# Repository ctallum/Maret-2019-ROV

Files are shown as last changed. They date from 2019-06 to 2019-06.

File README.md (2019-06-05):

# Maret 2019 ROV
In this Git Hub, I will try to provide all the needed code, 3d model files, and instructions needed to either build or fix the 2019 ROV. 

## Code
### Setting up the Rasperry Pi 

To set up the Rasperry pi, first make sure the Pi has a static IP adress. If it does, skip ahead. If it doesn not, you will not be able to ssh into the Pi. To set a static IP address, first type the following into the Pi terminal.
```bash
sudo nano /etc/dhcpcd.conf
```
At the bottom of the config file, type the following:
```bash
interface eth0
static ip_address=169.254.38.217/24
```
This should create a static IP address on the Pi. (The IP adress doesn't need to be the one written above. If you make your own, just make sure to change the code in the Poolside.pde to reflect this). You can check everything works by typing the following into the terminal.
```bash
ifconfig
```
Under eth0, it should report the static IP.

The next step is to make sure the Pi has all the needed python libraries. You will need Nanpy and Flask. To install Nanpy, type the follwing into the terminal.
```bash
sudo pip3 install nanpy
```
To install Flask, type the following into the terminal. 
```bash
sudo pip3 install flask
```
There are many installation guides online (including the one on Flask's website) that involve the creation of virtual enviorments for python. This is not nescessary. Disreagard these guides and just install flask with the above method. 

To finally get the code up and running, on the Raspberry Pi desktop, you will need the folder titled "New". This folder contains all the Pi code to get the craft running. I will include this folder with all its contents in the GitHub. All the code is written to be run in python. 

### Setting up the Surface Computer
On the surface computer, you will need the folder titled "Poolside". This folder contains all the code that runs on the surface. I will also include this folder with all its contents in the GitHub. The "poolside" code runs in a program called Processing, so also download that. In Processing, you will need to add the following libraries: G4P, Game Control Plus, and HTTP Requests for Processing. Adding these libraries is really easy. In processing, "Open Library" --> "Add library...". From here you can search up each library and add them. You need to install the Xbox controller drivers. 
- https://processing.org/
- https://www.techspot.com/drivers/driver/file/information/15363/

### Setting up the Arduino
Contrary to popular beleif (or at least what we thought we knew) you do indeed need to set up Nanpy code on the Arduino. You can follow the guide below for full instructions on installing the nanpy code on the Arduino. 
- https://nanpy.github.io/

Alternativly, you could plug the current arduino into a laptop, open up the Arduino software, save the contents as an ide. and then copy the code onto another Arduino. (I haven't tried this in person, but I think it would work, and it would save you a bit of time).

# Running the ROV

First, make sure everything is properly connected. In the ROV, the camera should be plugged in fully (and beleive me, it is easier to check now than it is to change it later once the dome is on). On the surface, the ethernet and Xbox controller should be plugged into the surface laptop. The tether should be plugged into 12 volts.
 
The first step in running the ROV is to run the code on the Pi. Since the Pi is on the craft, you must run the code remotely. This is done via ssh. On a windows machine, one could use a program such as Putty to ssh to the Pi, however, on a Mac, you can use the built in Terminal. 

First, establish connection with the Pi. 
```bash
ssh pi@169.254.38.217
```
169.254.38.217 is the static IP address of the Pi we have used in years past. However, if the physical Pi changes or you change the software, the IP may be different. You can always find the IP address of the Pi by typing "ifconfig" into the Pi terminal. You can also change the physical IP adress of the Pi by edditing the dhcpcd.conf file (see the link below). (Also see above).
- https://www.modmypi.com/blog/how-to-give-your-raspberry-pi-a-static-ip-address-update

Once you have connected to the Pi, it will request a password. On a new Pi, the default password is "raspberry". However, if Chris L. is the one who set it up, the password will probably be "hi".

Once you are into the Pi, you need to access the run file.
```bash
cd Desktop/New/ROV
```

This will put you inside the ROV subfile within the New folder. Inside this folder is the file App.py. This is the main code which runs the ROV. Run this file.
```bash
python3 App.py
```

As the file runs, the Terminal screen will display what is currently going on. It should say something along the lines of setting up a nanpy connection and running a flask server on the ip address "0.0.0.0:5000". (Don't worry that it says 0.0.0.0 and not the IP adress of the Pi, this if fine. 0.0.0.0 is the local adress of the Pi which is the IP you set). The Terminal screen is also the Debugger window, so if anything goes wrong, it will tell you. Keep this window up. 

After you have run the Pi code, you need to run the Poolside code. To do this, open the PoolSide folder and open the file titled PoolSide.pde. This file should open up in Processing. In processing, click the "Run" button. This should bring up a small window that gives the readings of all the motor values. 

To get the video streaming site up, go to your web browser and type in:
```bash
http://169.254.175.59:5000
```
This should open up a webpage with the live video stream. 

### Tips and other helpful bits
- When trying to ssh into the Pi, it may not be immediate. Just spam the ssh request until it goes through.
- If you you are testing the Pi out (and the Pi is not in the tube), you can run the program manually without ssh. To do that, hook up a monitor and keyboard/mouse to the pi. You can edit the code by oppening the App.py file in the python scrip editor, but you cannot run it like you might be used to doing with any other python program. If you run it from the python scrip editor, you cannot stop the program from running without rebooting the Pi. If you want to run it to test it out (or test out any changes you made to it), you have to run it from the terminal. 
```bash
cd Desktop/New/ROV
python3 App.py
```
- Always run the poolside code after the Pi code is running. 
- I don't think it is nescessary to runn the poolside code to access the live video stream, but that is the only thing you can do. 

# Electronics

## Componenents
- Rasperry Pi [buy link](https://www.amazon.com/ELEMENT-Element14-Raspberry-Pi-Motherboard/dp/B07BDR5PDW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)
- Arduino Mega [buy link](https://www.amazon.com/Elegoo-EL-CB-003-ATmega2560-ATMEGA16U2-Arduino/dp/B01H4ZLZLQ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)
- Pololu mc33926 motor drivers (x6) [buy link](https://www.pololu.com/product/1212)
- 12v to 5v buck step down converter (x2) [buy link](https://www.amazon.com/DROK-Electric-Converter-Step-down-Regulator/dp/B00C63TLCC?ref_=fsclp_pl_dp_2)
- dsn-vc288 Volt Amp Meter [buy link](https://www.amazon.com/McIgIcM-Digital-Voltmeter-Ammeter-10ADetector/dp/B06XR2XKNT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)
- Screw terminals [buy link](https://www.amazon.com/Eowpower-Position-Terminal-Insulated-Barrier/dp/B06XKFCTSM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)

## What they do
Rasperry Pi
- This is the brains of the ROV. It handles all the inputs from the surface. The video feed also runs through the Pi. 

Arduino 
- The Arduino is what is considered a "slave" to the Rasperry Pi. It only serves as an extension of the Pi. Since the Pi has limited output pins, and it needs to control 6 motor controllers and a few servos, it uses the Arduino to send out the signals. The Pi sends instructions to the arduino such as "set pin 30 to HIGH" or "set pin 6 pwm to 125". The  Arduino follows these instructions. In total, the Arduino manages 8-9 digital outputs (on or off) depending on how many servos we are running, and 6 analog outputs (pwm 0-255).

Pololu Motor Drivers
- We are using 6 motor drivers, one for each pilge pump motor. You can think of these motor drivers as a gate. They control how much voltage goes to the motors, and, as a result, their speed. They take inputs from the arduino which indicates the speed of the motors and in which direction the motors spin. 

12v to 5v Converters
- The different electronics on board require different amounts of voltage to run, some 12v and some 5v. The craft is supplied 12 volts from the surface (through the tether). The converters simply drop the 12 volts down to 5 volts for the electronic that need it. 

Screw Terminals
- Electronically, they serve no purpose. However, they make wiring a lot easier. One of the Terminals is for 12v and the other 5v. The rows alternate positive and ground. 

Volt/Amp meter
- this gives a vidual indicator of how much voltage and amperage is running though the system. The voltage reading should always give 12.00V (or close to it). The amperage reading depends on how fast the motors are running and if the servos are currently being used. Idealy, the amperage should stay way below 20A.

## How to wire the ROV
### Power management

The Rasperry Pi should always run on 5V. Typically, we give it its own 12-5V step down coverter, hooked right up to the 12V mains. This should give it the cleanest 5V power. We currently run the power though the GPIO pins on the Pi. In our circumstance, this is the easiest way to give power to the Pi. Alternatively, you could power the Pi though the micro USB port. 

We have the Arduino running on 12V hooked up to the 12V bus. There are many different ways to power the Arduino. In a pinch, the Arduino can be powered directly by the USB data cable, under heavy load, this is not sufficient. You can also run the Arduino with 5V by plugging the 5V into the 5V pin and the ground into the ground pin. This should work perfectly fine in almost all cases. Lastly, you can power the Arduino the way we do it. You can power the Arduino through the "vin" pin with any voltage between 6 and 12V. (The ground line still goes to ground). We run 12 volts into the "vin" pin. We did this in the off chance that one of our 12-5V converters breaks. If that happens, the Arduino would fail. However, there will amost always be steady 12V power, and even if this 12V is not perfect, we have a bit of leeway. 

The motor drivers are the most complicated it terms of power wiring. They require both 12V and 5V. The 12V is reserved for the motors, and the 5V is for the chip that does all the logic. On the proto board to which the six motor drives are soldered, there are is a 5V and ground wire set attached. These should go to the 5V bus. On top of each motor driver, there are four screw terminals. Two of these are where the motors connect, the other two are where you need to run 12V. On each motor driver, there is a set of wires. One goes to 12V, the other ground. Use the 12V bus. 

All the servos run off of 5V. The red and black lines of the servo should alwasy go to the 5V bus. 

The volt/amp meter is rather confusing to wire in. I will include an image below. To wire the volt/amp meter, the small black and red wires should go directly to the power lines in the tether. The small yellow wire should also go to the postive line on the tether. The big black line of the meter should also go to the ground line in the tether. The 12V power bus line should go to the positive line on the teter. Here is where it gets weird, connect the ground line of the 12V power bus to the big red line of the meter. This may look like cross-wiring, but it is fine. Just follow the diagram. 
diagram

### Data management

Connect the ethernet in the tether to the ethernet port of the Rasperry Pi

Connect the Rasperry Pi to the Arduino via a USB type A to USB type B cable. This cable comes with the Arduino in the box.

Connect the Arduino to the motor drivers via the two rainbow colored ribbon cables. One controls the speed of the motors, and one controlls the direction of the motors. Follow the diagram below. Idealy, there would be three cables, the last one being data feedback; however, we have never set this up in the code, and it is not particularly helpful. 

[insert diagram]

# Current Issues / Things to do next year
### Mechanics
- Shorten the wires that go to the motors
- Create a new camera mount that attaches to the electronics tray, not the front flange. Make sure that you can access the micro-SD card with the mount. 
- Add the front and back circular supports for the electronics tray

### Code
- For some reason, there is one motor that runs slower than the others. It doesn't spin under low voltage, and runs slower than others at heigher voltages. My guess that it has to do with motor controller. Maybe replace it.
- The right and left strafe are backwards. On the controller, when you move the left joystick to the left, the rov shifts right, and vice versa. This is because I rotated the motor controller protoboard 180 degrees. The drivers that used to run the left motors now run the right ones, and vice versa. To fix the issue, go into the App.py file and change around the pin order in the lists. 
- One of the motors doesn't change direction. I think this is again due to issues in the code with the pins.

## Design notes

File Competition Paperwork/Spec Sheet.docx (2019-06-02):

SIPHONOPHORE

Maret School, Washington D.C.

Team Information

Founded in 2014

Consists of 9-12th graders

Has participated in the Mid-Atlantic Regional competition yearly since 2015.

Team Members

Chris Allum Owen Crise Chris Laporte Tsubasa Shima Clarissa Cantacuzene Clara Caspard Liam Esparraguera Grace Noll Kannan Ramasawmy Reese Alpher Ben Schroeder John Jai Reyna Pratt Jennifer Groppe | Co-Captain, Junior, 80 hrs Co-Captain, Junior, 70 hrs Co-Captain, Junior, 80 hrs Design, Senior, 60 hrs Mechanics, Sophomore, 60 hrs Mechanics, Sophomore, 60 hrs Software, Sophomore, 60 hrs Software, Sophomore, 60 hrs Electronics, Sophomore, 60 hrs Electronics, Sophomore, 60 hrs Design, Sophomore, 60 hrs Mentor Mentor Mentor

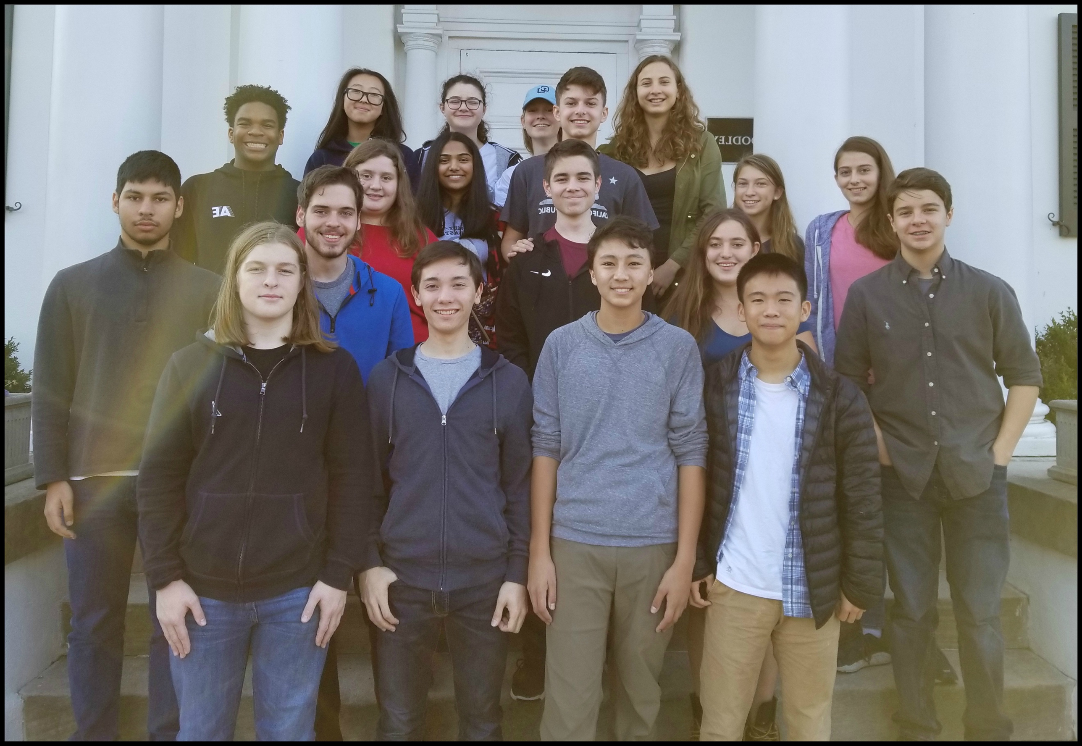
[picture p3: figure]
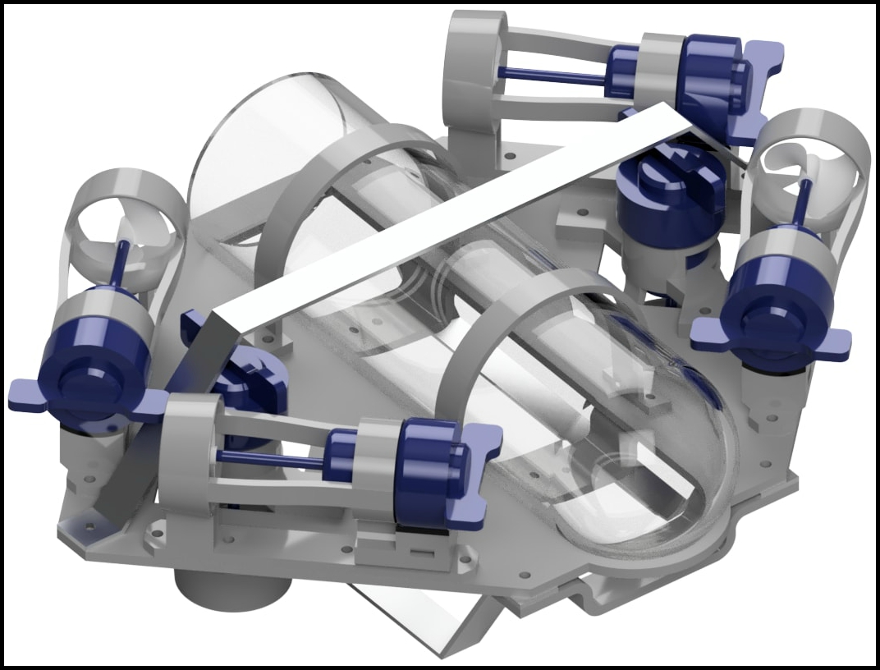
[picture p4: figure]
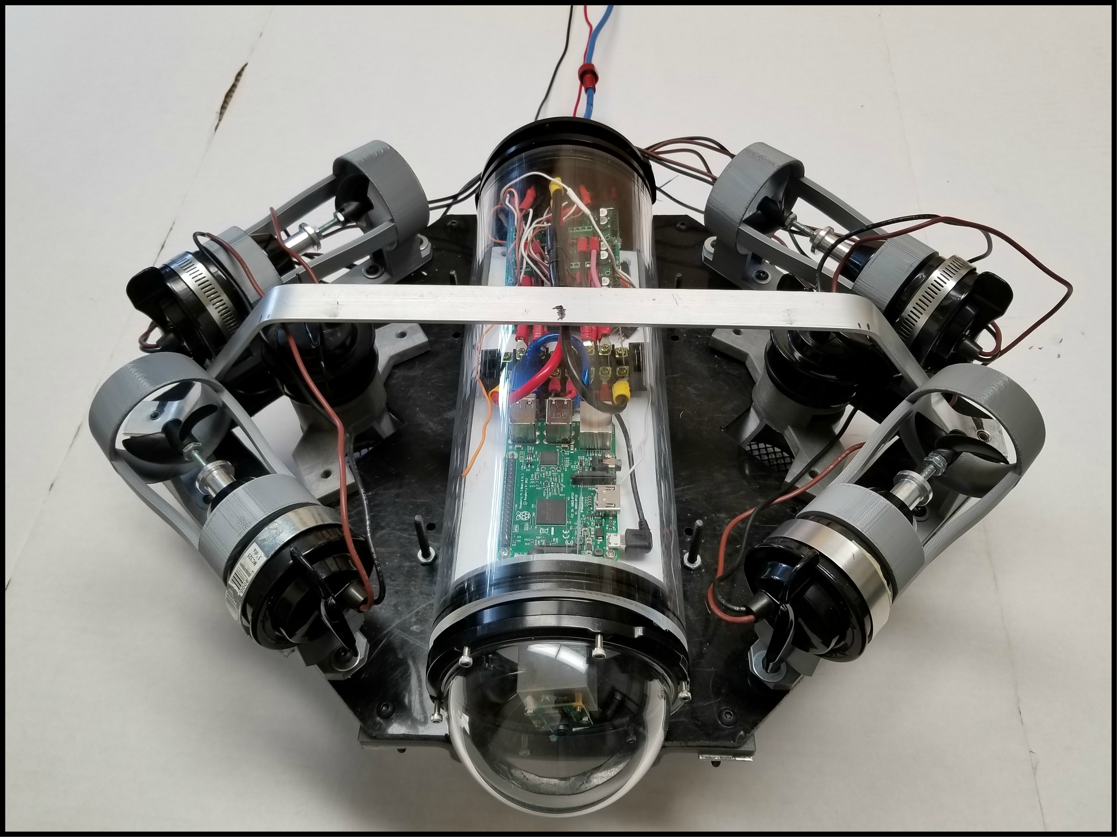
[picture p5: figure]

ROV Specifications

Name: Man o’ War Weight: 7.5 kg. Dimensions: Width: 50.8 cm Length: 39.6 cm Height: 18.4 cm Tether Length: 30 m Cost: $ 1,100 | Special Features: 4-axis ROV control, rotating claw, 3D printed motor mounts, onboard Raspberry Pi, easy expandability for both servos and cameras. Safety Features: Fully covered propellers, 30A fuse, tether strain relief, no sharp edges, clean wiring.

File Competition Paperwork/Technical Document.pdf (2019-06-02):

# SIPHONOPHORE

## Maret School, Washington DC Mate ROV Competition Technical Documentation May 12, 2018

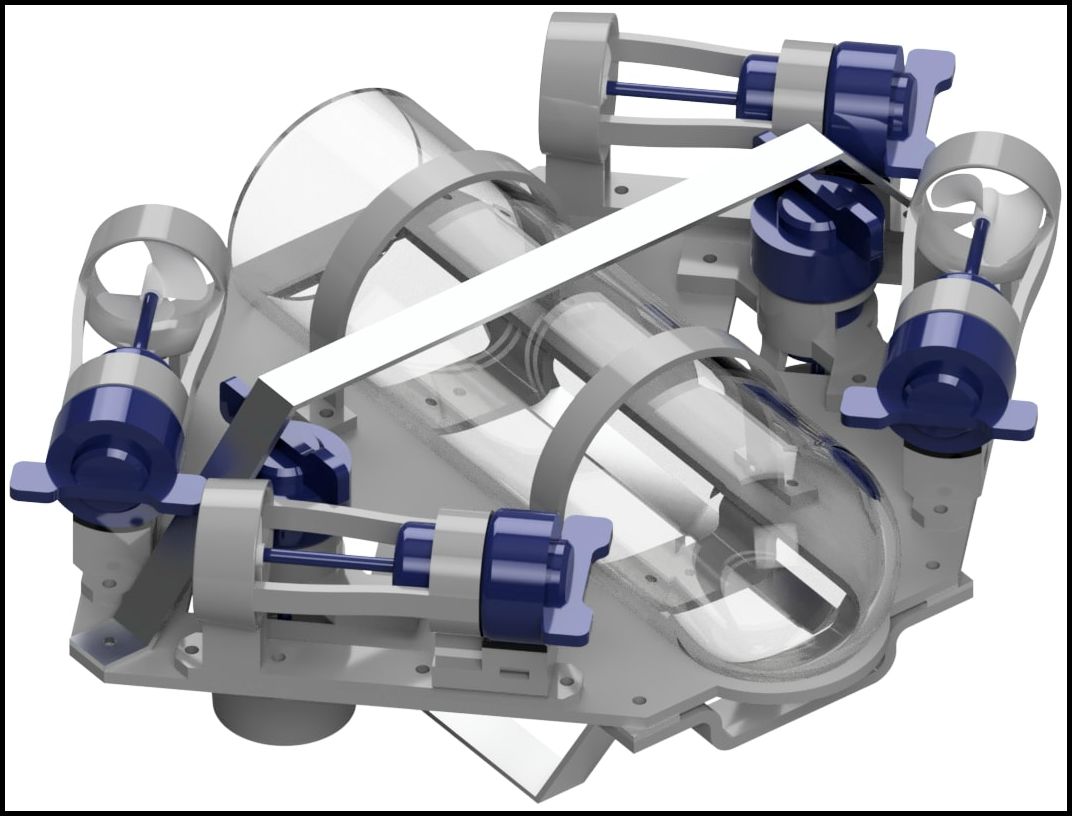
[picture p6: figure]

Chris Allum
Owen Crise
Chris Laporte
Reese Alpher
Clarissa Cantacuzene
Clara Caspard
Liam Esparraguera
Grace Noll
Kannan Ramaswamy
Tsubasa Shima
Ben Schroeder

John Jai
Reyna Pratt
Jennifer Groppe

Co-Captain, 3rd year
Co-Captain, 3rd year
Co-Captain, 3rd Year
Electronics, 1st Year
Mechanics, 1st Year
Mechanics, 1st Year
Software, 2nd Year
Software, 1st Year
Electronics, 2nd Year
Design, 4th Year
Design, 2nd Year

Mentor
Mentor
Mentor

## Abstract

The goal of Siphonophore is to produce a Remotely-Operated-Vehicle (ROV) to perform tasks in environments in which it might be unsafe or difficult for humans to operate. Our ROV has been crafted to tackle the challenge of restoring the water of the Pacific Northwest as well as to research the ever-changing underwater activity. Specifically, our ROV has been designed to locate and return the wreckage of sunken airplane to the surface, to install and recover an ocean bottom seismometer, and to install a tidal turbine to monitor underwater currents. To accomplish these tasks, on our ROV, we have installed a rotating claw for general use, two cameras (one of which rotates a full 360 degrees) for observing the surroundings, and a set of tools specifically designed to accomplish each individual task. Furthermore, our ROV is designed with mobility in mind. The size and weight allow it to move smoothly through the water without hindrance, and its four-axis control allows the user to easily control the ROV in complex maneuvers. This is the fourth consecutive year Siphonophore has returned to the Mate ROV competition, and each year we strive to do better the previous. Our team is constructed of eleven members, and each of us has worked tirelessly to put forth the best possible ROV.

## Table of Contents

Abstract | 1
Team Information | 3
Safety | 4
Safety Checklist | 4
Design Rationale | 5
Overview | 5
Mechanics | 6
Electronics | 8
Code | 9
Finances | 10
Budgeting | 10
Cost | 11
Reflection | 12
Problems Encountered | 12
What We Could Have Done Better | 12
Future Improvements | 13
Appendix | 14
SID | 14
Software Flowchart | 15
Finances Chart | 16

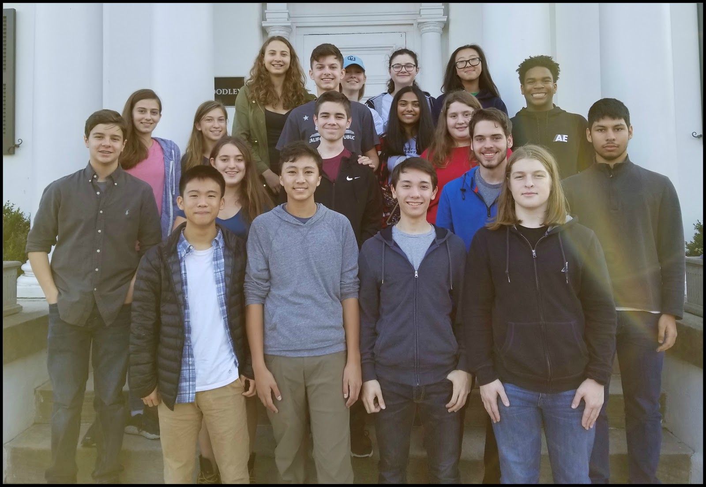
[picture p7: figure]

## Team Information

Siphonophore was founded in 2014 and we have attended the Regional MATE ROV competition yearly since 2015. With this attendance, our team has years of experience behind our efforts. Our three captains each have participated in the Mate ROV competition for three years, and the rest of our team’s experience range from it being their first year all the way to their fourth year. However, through time, our team management and leadership system have remained fundamentally the same. At the core, our team is split into three subgroups, each designated to focus on one aspect of the ROV: mechanics, electronics, or coding. Every member of Siphonophore gets to choose the group that they are a part of, and also has the option to change groups if they so desire. Each subgroup is headed by a captain who has the most experience out of that group and who can provide a leadership role. These three captains co-run Siphonophore as a whole. To maximize the efficiency of the Siphonophore, although the subgroups are distinct from each other, each interacts heavily with the others, sharing ideas and working on common problems from their own perspectives. Furthermore, the captains of each subgroup meet weekly to discuss the direction the team as a whole is going and what work needs to be done that week to maximize productivity. We have found that this system provides a robust structure of leadership, while also allowing individuals to delve into the subjects that they are most passionate about.

## Safety

As a team, we take the issue of safety very seriously. We try to ensure that at all times, both during the construction of the ROV and during its operation, the proper precautions are in place so that everybody is safe. When constructing the ROV, anytime one is dealing with power tools, the individual must be wearing eye protection and be supervised by someone else with adequate experience. Furthermore, when dealing with potentially harmful materials, such as epoxy, or using equipment that could cause harm, like a soldering station, we require that the individual understands the potential risks and is taking the proper precautions to ensure both their own and other’s safety.
In ensuring the safety of everyone involved, we also strive to create an ROV that is safe for anyone to operate or work with. Foremost, we ensure that no part of the ROV exterior can cause harm. We have covered the propellers in a shroud
and mesh so that it is impossible to touch and injure
oneself with the propeller when it is spinning. In
addition, we have also covered or smoothed out any edges or part of the ROV that might be deemed sharp or capable of causing injury. On the tether, we have placed
a strain relief system so that any sudden tugs of the line
will not cause damage to the ROV. In terms of

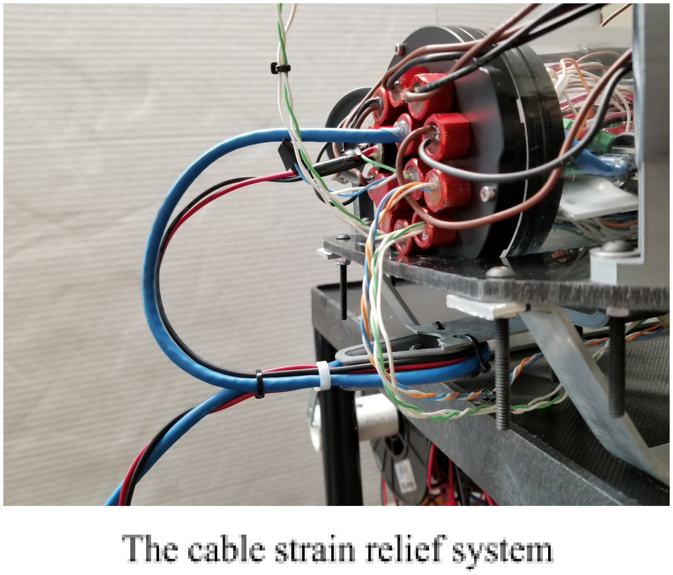
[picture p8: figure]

electronics, the tether contains a 30A fuse to prevent any dangerous electrical issues that might occur in event of a malfunction. We have also built in a system-wide kill switch that will shut down all motors in case of an emergency in order to prevent injury to those who might be working with the ROV. Furthermore, all wiring inside the ROV is clean and there are no exposed wires.

### Safety Checklist

### 1. During Construction

a. Safety glasses must be worn while using power tools
b. The individual is supervised when using power tools c. Before using all power tools, proper trained must be accomplished
d. Gloves and a dust mask must be worn while dealing with epoxy
e. Appropriate clothing must be worn at all times
f. Proper workshop behavior (no fooling around) at all times

### 2. During Operation

a. No wiring is exposed and all wiring is secured
b. Waterproof enclose is securely closed
c. All mechanical fastenings are secure; no loose bolts or nuts
d. There are no sharp edges
e. Propellers are covered
f. Tether is coiled properly and is not a tripping hazard
g. Deck crew is appropriately dressed
h. Deck crew is prepared for launch

## Design Rationale

### Overview

For the past two years, the design for our ROV has centered on the use of a waterproof plexiglass tube purchased from Blue ROV. After failed attempts to manufacture our own waterproof boxes, we concluded that the best option was to look for an off-the-shelf option. This tube contains all the electronics as well as a camera and is centered in the middle of an HDPE deck. Positioned around the
central tube are six bilge pump motors, four for lateral
movement, and two for vertical. We have used these

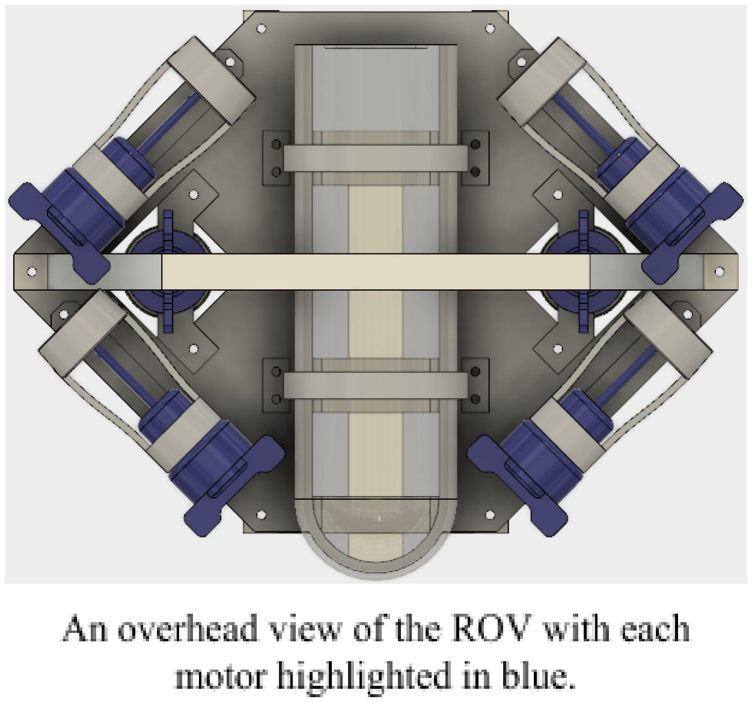
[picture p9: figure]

motors for the past few years because of their continued reliability, power, and ease of use. Furthermore, our decision to use six motors stems from the desire to keep the ROV as simple as possible while maintaining the capacity to move freely and efficiently. The four lateral motors are arranged in a vector layout so that the ROV can move forward and back, strafe side to side, and rotate. Over years of experimentation, we have concluded that this layout is optimal in terms of maximizing mobility and simplicity. Some of our early design inspirations came from the form of stingrays. We noticed how their diamond shaped body lends itself well to a vectored motor layout. We also gained the inspiration to mount everything onto a single plane from the observation that their flat bodies allow for a streamlined movement.

Another important design choice was to
maximize ease-of-use. Rather than using a complex
surface control station, often including many computers, monitors, and joysticks, we have opted for the simplest solution possible. On the surface, our ROV is connected only to a single laptop to which an Xbox controller is connected. We have found that these two devices are sufficient for the
purpose of controlling the ROV. The single Xbox
controller directs all the motors, the claw, and the

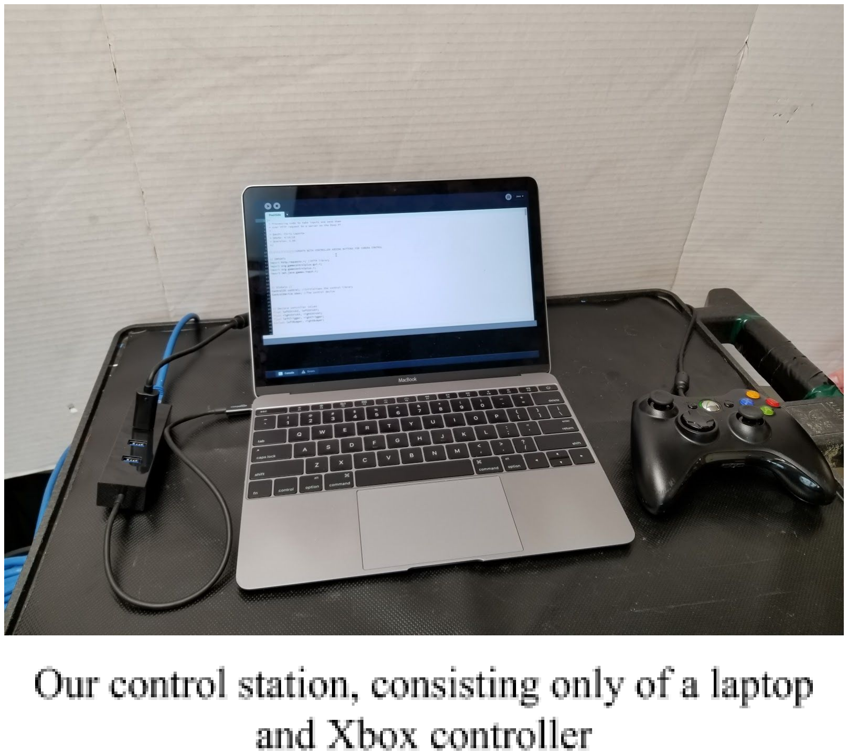
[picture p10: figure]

cameras, while the laptop sends over the data and projects the live video feeds from the ROV. To make this possible, a significant amount of the motor and camera data is processed on the ROV itself. Onboard, we have both a Raspberry Pi and an Arduino. Both control all ROV related operations. Not only does this decision lend itself to ease of use, but it also reduces the number of wires running in the tether to only a power line and an ethernet cord. This lightweight tether again reflects our desire for a simple, yet highly mobile ROV.

### Mechanics

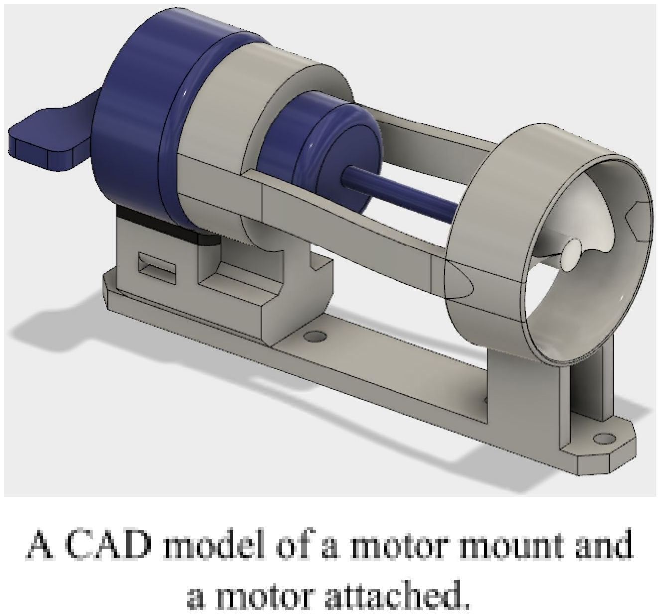
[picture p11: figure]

One of the major improvements of our ROV this year is our new 3D printed motor mounts. We decided to design our own mounts because after looking what was available on the market, we concluded there was nothing that satisfied our specific needs. We needed the mounts to be able to secure a bilge pump motor onto a deck and be able to cover the propeller, all in one piece. We were able to custom design a motor mount to do all of these tasks. In last year’s design, we used two pieces, one to mount the motor and another to cover the propeller. This choice resulted in the overall design having more give, and caused the propeller to occasionally rub against the motor shrouds. To fix this, we changed the design so that the mount and the propeller shroud were one piece. Although this change increases the time it takes to print the motor mounts, we concluded that it was well worth it.

Another feature of our ROV that we have
drastically improved is its claw/manipulator. We
decided to buy a claw rather than to build one because we concluded that either 3D printing one or constructing it by some other method would result in it being too flimsy and wouldn't provide us any benefits over a store bought one. This claw was a much needed
upgrade to our previous solution. Our previous claw

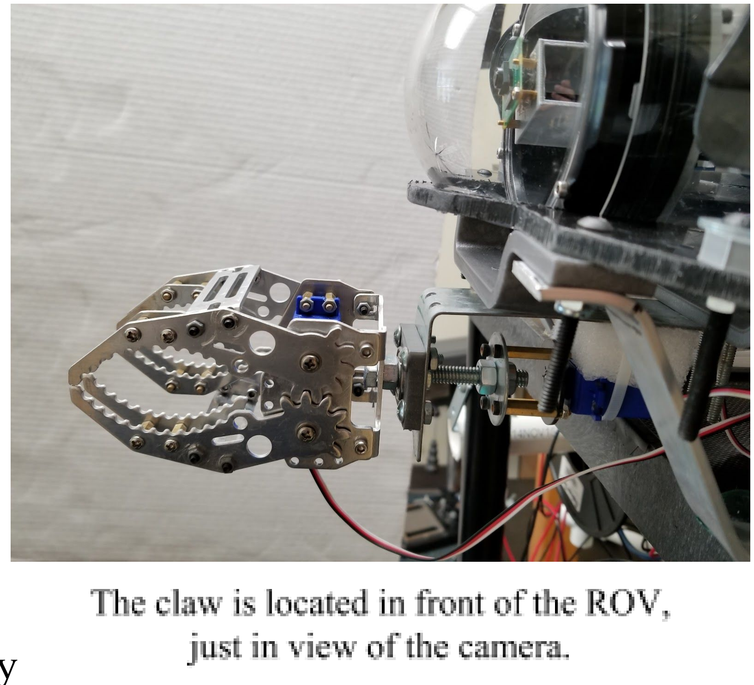
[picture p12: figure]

had issues opening and closing due to its badly
manufactured parts; many of the bolts did not line up properly and caused the claw to be severely misaligned. This claw is much better built and opens and closes much more smoothly due to its use of two ball bearings. Furthermore, to this claw, we added a rotating wrist. This allows our ROV to grasp both vertical and horizontal objects. We decided to add this wrist after watching many of the simulated ROV run-throughs on the MATE ROV webpage. We concluded from the videos that only with a rotating claw could we grasp all the objects underwater. Both the claw and wrist use waterproof servos to operate.

To allow the greatest usability of our ROV, we have two cameras onboard. The first of which is the Raspberry Pi camera module. This camera is mounted on a 3D printed bracket on the inside of the waterproof tube. This camera overlooks the claw and allows the user to use to see the surrounding of the ROV from a first-person point of view. The second camera we use is a waterproofed Logitech webcam. We decided to use this camera for its high quality video quality and its relatively small size. We waterproofed this webcam by taking it apart until we had just

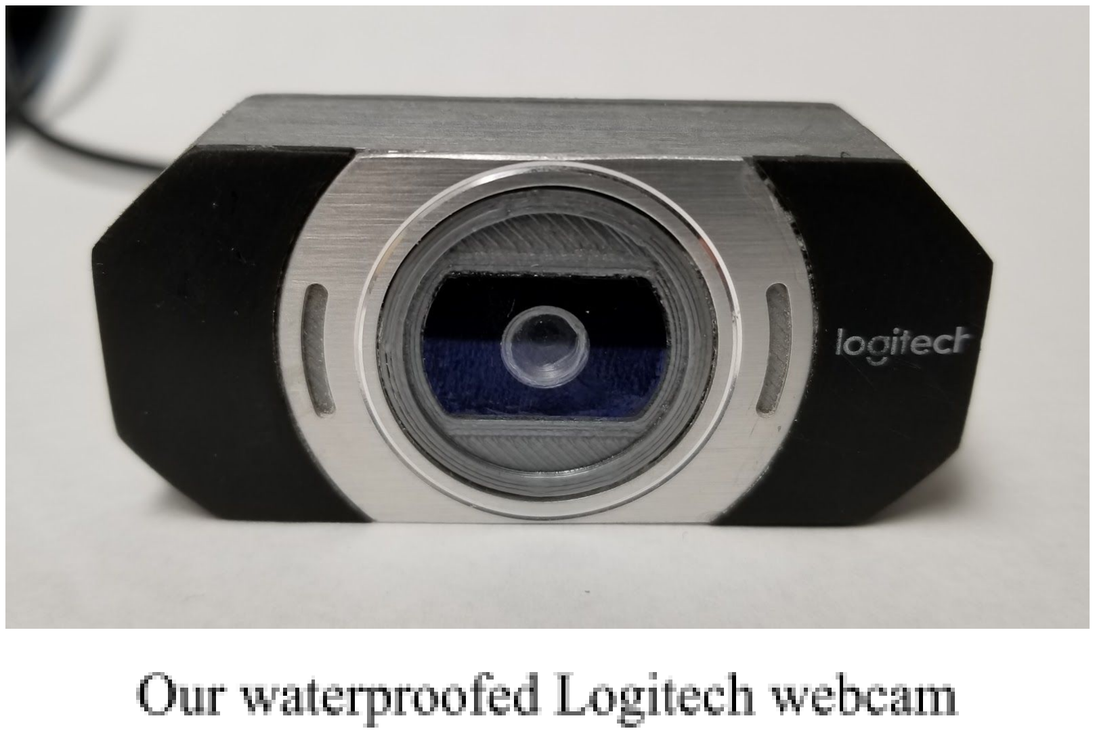
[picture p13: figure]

the internals. We then 3D printed a new enclosure in which the electronics would sit. To waterproof the electronics, we potted them in silicon and glued the enclosure shut. To maintain the aesthetic look of the original camera, many of its original enclosure pieces have been taken apart and glued to the new 3D printed enclosure. This camera sits on top of the ROV and rotates to give a full 360 degrees view of the craft.

### Electronics

There are three essential components to the electronics system: the Raspberry Pi, the Arduino, and the motor controllers. We use the Raspberry Pi for two functions: the camera feeds and data. Firstly, we have two cameras that run into the Raspberry Pi, one of which is the Pi camera module, the second is a waterproofed USB webcam. These camera feeds are sent over by the Raspberry Pi to the surface laptop. Secondly, all data that comes from the surface is processed on the Raspberry Pi. This includes motor and servo data. From the Raspberry Pi, this data is transferred to the Arduino. In this system, we do not use the Arduino for any computation, but rather as a way to distribute the data among
the motor controllers and servos. Because the
Raspberry Pi has a very limited number of data
pins, we instead use the Arduino to send and receive the following data: motor speed values, motor direction values, motor feedback values and servos values. These motor speed and direction values are then fed into a set of six Pololu H-bridge motor drivers which are all

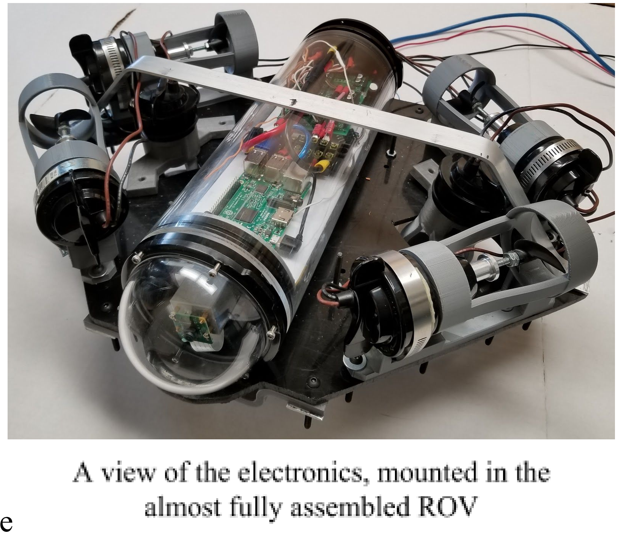
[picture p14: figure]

soldered onto a single PCB board. From these, the motors are directly controlled. These motor controllers also record the current draw from each motor send back the data to the Arduino and subsequently the Raspberry Pi. The motor feedback data allow us to spot any discrepancies and allow us to prevent any issues as promptly as possible.

To power our ROV, we run in a single 12V line into the back of the tube. This 12V is first distributed into a bus which allows for all the other components to be easily connected. From the 12V bus are powered the motors, the Arduino, and two 12 to 5V step-down buck converters. One of these step-down converter leads to another bus, which distributes 5V to all the servos, and the motor controllers. The other leads directly to the Raspberry Pi. We use two step down converters because of our long history of power management problems. Due to the fragility of the Raspberry Pi, any disruptions in power force it to restart, causing our ROV to crash. To solve this issue, we have one step down converter specifically dedicated to the Raspberry Pi. Through this, we can minimize any power disturbances that might influence that might cause a crash. Another issue we have had in the past is managing to power the Arduino under heavy stress. Although the Arduino can be powered directly off of it’s serial connection to the Raspberry Pi, this connection limits the amount of current it can draw. This is why we power the Arduino directly off of the 12V bus, so that it is not limited by the current draw limitations of a serial connection.

### Code

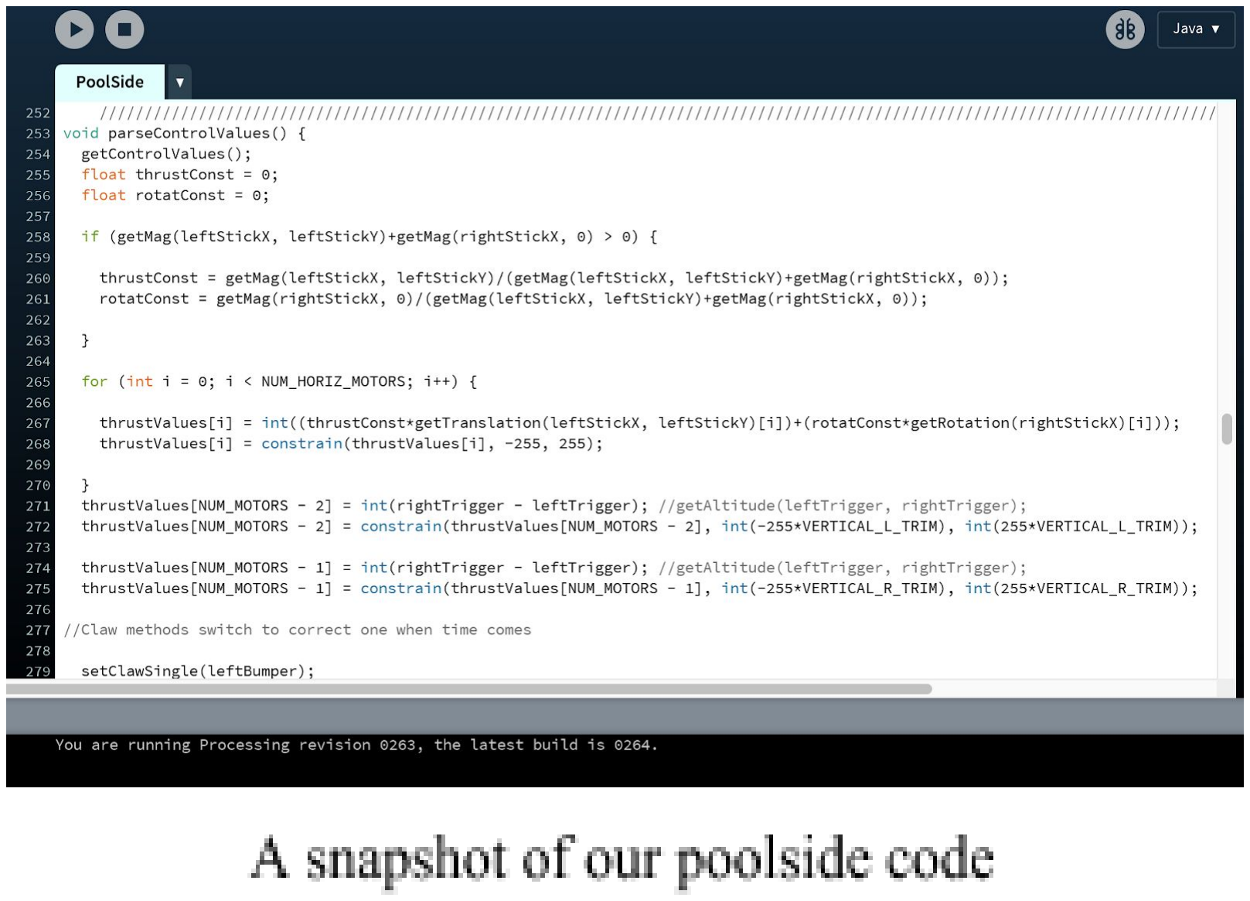
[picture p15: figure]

The code follows a very simple and straightforward data flow. We use processing, a programming language derived from Java, on the poolside computer and Python on the onboard Raspberry Pi. Within processing, we use three libraries in order to fulfill our needs. In order to take and use inputs from our Xbox controller, we use the libraries G4P and Game Control Plus. We then take these inputs and use vectors to convert them to values which we can send to the motors. We then use our third library, HTTP Requests for Processing, to send the motor and servo values in different MultiDict groups to a web server running on our Raspberry Pi.

The web server is run through a Python microframework called flask. It allows us to send and receive data through HTTP commands. This key step allows us to use ethernet instead of a serial connection between the poolside computer and the onboard systems. The framework also lets us run our video feeds through a website accessible over ethernet from the poolside computer. Using the built-in library, Picamera, we create a class and an object which takes individual frames from the cameras and displays them on the flask webpage without having to store the pictures in memory. The motors and servos are each fed data on flask through a webpage which corresponds to their function. The motors and have a flask page, and so do the two servos associated with the claw. By using multiple pages in flask instead of one, the data can be parsed through more efficiently and the code is more legible and easy to work with.

The data is then sent to the Arduino through a library called nanpy. Its serial manager functions allow for the Raspberry Pi to operate the Arduino as a slave board without ever having to have any specific code on the Arduino. This makes the code much easier to work with as we can access the Raspberry Pi through SSH or other forms of remote desktop without having to pull it out of the waterproof enclosure. In addition, this means that we do not have to work with Arduino code, and instead only have to work with Flask and Python which allows for greater expandability within our system.

## Finances

### Budgeting

Whenever we construct a new ROV, we try to keep our overall expenditure low by reusing what is possible from the previous year’s ROVs. This year, that meant reusing most of the same electronic components, and the same waterproof tube from our previous ROV. We also were able to use most of the same construction materials since they had not yet been entirely used up. With this approach, we are able to keep our costs to a minimum.

Nonetheless, the beginning of the year, Siphonophore was allotted $1,500 by the Maret school in order to design and construct our ROV. With this money, we split it among our subgroups and also set aside a significant portion of the money for the construction of props. We allocated $300 to the mechanics subgroup because in the past we have found this group to use up the most money, purchasing new building materials and off the shelf parts. We anticipated any new additions that this subgroup might make would be the most expensive. We also allocated a sum of $200 to the electronics subgroup in case that some of our reused electronics break. Lastly, we allocated $100 to the coding subgroup; however, we did not expect this sum to be used up because the writing of code does not require any purchases. The remaining majority of the fund was left unassigned, either to be used for building props and task solutions or for any subgroup if they ran out of money. In terms of travel costs, our team saved money by driving a van from Washington to Philadelphia, resulting in our only expenses to be accommodations and gas, which we estimate to be around $550 for the entire team. This sum of money is provided by the school separately from the initial $1,500.

### Cost

Our overall expenditure was much lower than our allocated budget, just around $560 in total for both the ROV and the props. In fact, the majority of this money was spent on constructing the props and designing task solutions. This was due to the fact that most of the construction materials had to be bought new and were not able to be reused from old projects. The mechanics subgroup used up the second greatest amount of money; however, they remained far under their $300 budget. Their spendings went primarily to replacing parts that were broken on the previous craft, such as the claw, servos, and the dome (which developed a crack after a drop). The mechanics subgroup also spent a portion of money buying new building materials such as aluminum bars and 3D printing new motor mounts. The electronics team used up the least amount of money, only $45.17. This was as expected since almost all the electronic components were reused. The money that was spent was used to clean up the wiring and to allow components to be more easily connected and detached. Some money was also spent buying a new camera. In total, although we spent far less than what we had available, we were still able to construct a high quality craft.

## Reflection

### Problems Encountered

One recurring problem that we encountered was with powering the Raspberry Pi. When we run the motors, they would draw extra current for a split second. This sudden draw would subsequently cause a brownout, causing the Raspberry Pi to crash and cease the program from running. We tried many solutions to fix this, and the only one that would work consistently was to isolate the Raspberry Pi electronically as much as possible. This entailed giving it its own step-down converter and a more direct line to the mains voltage. Fixing this problem wasted a huge portion of our time.

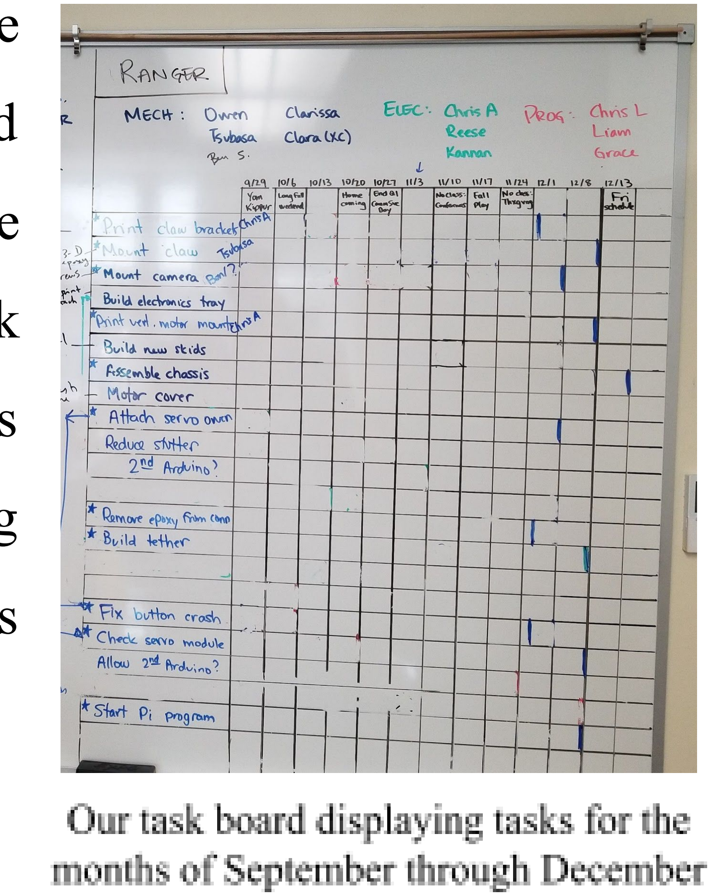
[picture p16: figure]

Another problem we had was getting everyone on the same
page in terms of what needs to be done. With so many people, and
only meeting a few hours a week, we needed to spend our time wisely. In previous years, we have tried to use an electronic task allocation system to keep everyone in time, but we found this system to be overly cumbersome. Our team found that it being online made it difficult to quickly access and that its layout was unintuitive. To fix this, we reverted to a simple whiteboard. On which, we drew a grid displaying which tasks need to be finished by which week. Although this system is old-fashioned, our team found it to be much easier to work with.

### What We Could Have Done Better

There are several things we could have done better this year. Firstly, it would have been much better if we were able to finish the ROV earlier. We finished our ROV only a few weeks before the competition itself. This was due to many last minute problems that we took too long to diagnose and fix. Although there was no way to foresee these problems, a more robust system of diagnosing and fixing the problem would have allowed up to fix the problems more efficiently. Instead, we spent weeks trying to fix simple problems, and that time could have been much better sent. One way we could have spent that time is by working more time on the individual ROV tasks. While we do have solutions for each of the challenges, if we had more time, we could have experimented with more complex solutions and could have possibly have created more sophisticated and efficient solutions. We could have also spent that time doing more pool tests, practicing the tasks and adjusting the ROV.

### Future Improvements

In terms of future improvements, our craft lends itself very well to changes. Our central tube has plenty of space left for additional sensors. Furthermore, our electronics layout allows for any added components to be easily added on. Some features that would be nice to add is an auto leveling system. We could use a pressure sensor to send depth feedback to the craft, and this would allow us to automatically fire the vertical motors to keep the same height. This would make it easier for the user to control, one of our primary goals. It would also be nice to have a better video stream page layout. While what we currently have is very functional, it would be nice to add a display that shows additional data such as which motors are currently running and what the position of all the servos are.

## Appendix

### SID

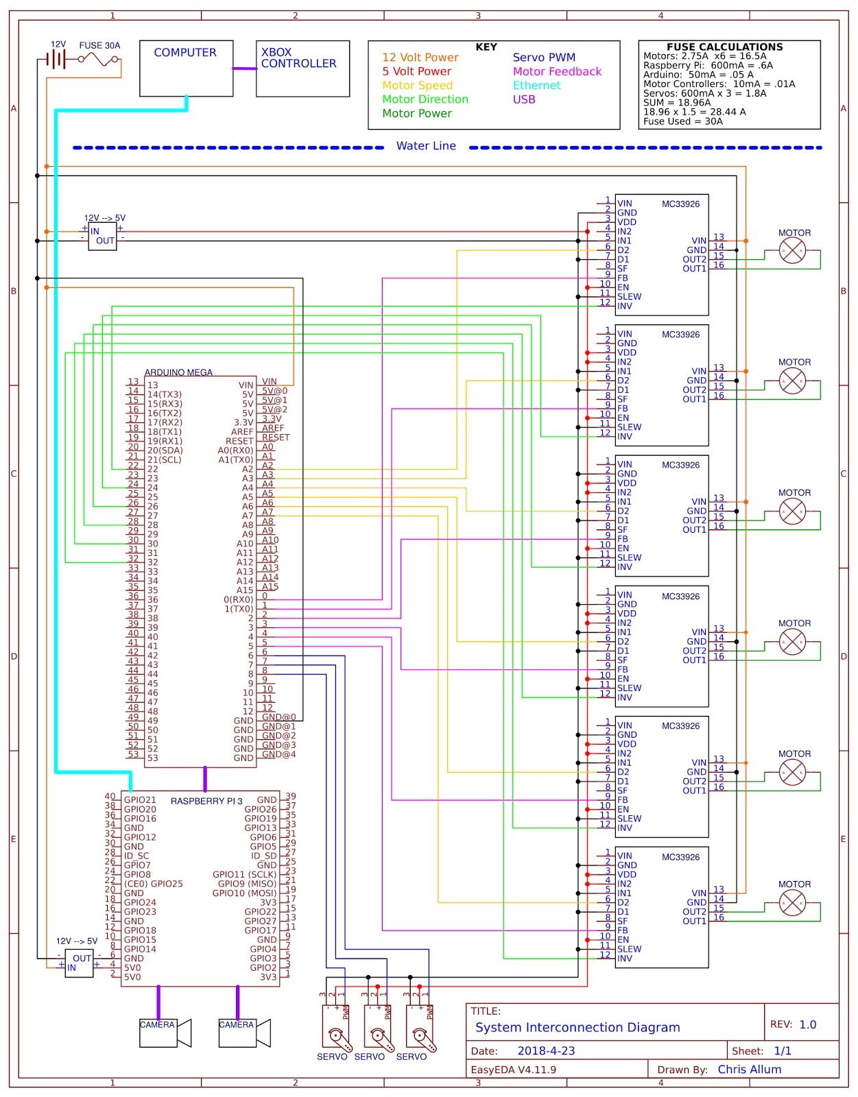
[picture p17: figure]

### Software Flowchart

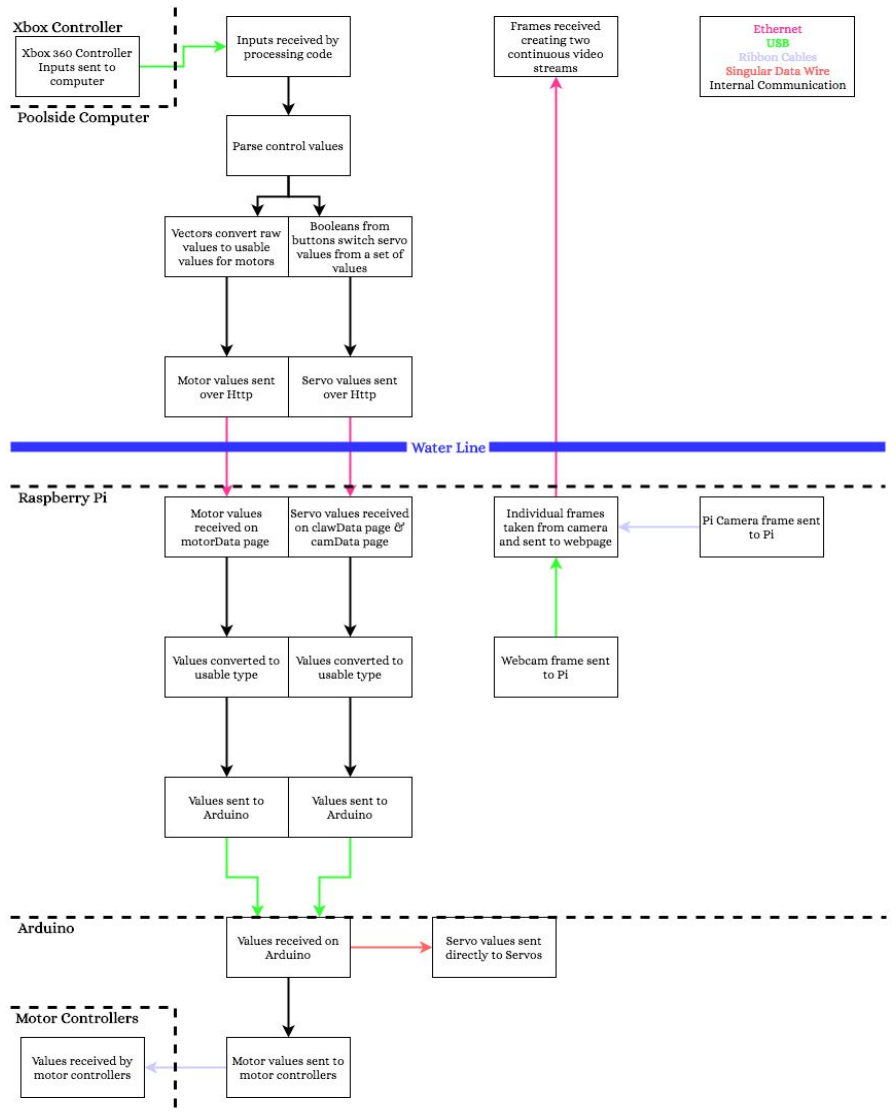
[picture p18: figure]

### Finances Chart

Item | Type | Price (USD) | Quantity | Total Cost | New Costs

Mechanical

Cable Penetrators | Re-used | 4 | 10 | 40 | 0
Cable Penetrators | Purchased | 4 | 4 | 16 | 16
HDPE | Re-used | 57.28 | 1 | 57.28 | 0
Tube | Re-used | 54 | 1 | 54 | 0
O-Ring Flange | Re-used | 29 | 2 | 58 | 0
Dome | Purchased | 59 | 1 | 59 | 59
Servo | Purchased | 26.13 | 3 | 78.39 | 78.39
Motors | Re-used | 30.62 | 6 | 183.72 | 0
Claw | Purchased | 25 | 1 | 25 | 25
Aluminum Bars | Purchased | 11 | 1 | 11 | 11
3D printed parts | Printed | 4 (estimate) | 6 | 24 | 24
Epoxy | Purchased | 9 | 2 | 18 | 18
Bolts/ Nuts / Fasteners | Re-used | 50 (estimate) | N/A | 50 | 0
Mechanical Totals | | | | $674.39 | $231.39

Electronics

Arduino | Re-used | 15.00 | 1 | 15.00 | 0
Pololu mc33926 | Re-used | 17.95 | 6 | 107.70 | 0
Raspberry pi | Re-used | 36.94 | 1 | 36.94 | 0
Proto board | Re-used | 2 | 1 | 2 | 0
Buck Converter | Re-used | 6.87 | 2 | 13.74 | 0
Internal Camera | Re-used | 28.85 | 1 | 28.85 | 0

External Camera | Purchased | 15 | 1 | 15 | 15
Screw Terminal Strip | Purchased | 2 | 2 | 4 | 4
Ethernet Cable | Purchased | 12.99 | 1 | 12.99 | 12.99
Wire Total | Re-used | 20 | N/A | 20 | 0
Ethernet Splitter | Purchased | 6.79 | 1 | 6.79 | 6.79
Barrel Jack converter | Purchased | 6.39 | 1 | 6.39 | 6.39
Electronics Totals | | | | $269.40 | $45.17

Props and Tasks

Polyurethane Air Hose | Purchased | 39.98 | 3 | 119.94 | 119.94
Giant balloons | Purchased | 12.29 | 1 | 12.29 | 12.29
Octopus Fishing Hooks | Purchased | 12.86 | 1 | 12.86 | 12.86
Straight Elbow | Purchased | 21.6 | 3 | 21.6 | 21.6
Brass Pipe Fitting | Purchased | 4.83 | 6 | 28.98 | 28.98
Amflo 701-2 | Purchased | 2.09 | 3 | 6.27 | 6.27
1/2in PVC Tee | Purchased | .46 | 12 | 5.52 | 5.52
1in to 1/2 inch T-joints | Purchased | 2.17 | 2 | 4.34 | 4.34
2 inches to 1-inch | Purchased | 1.67 | 3 | 5.01 | 5.01
1 inch to 1/2 inch | Purchased | 1.14 | 3 | 3.42 | 3.42
Braided Fishing Line | Purchased | 11.88 | 1 | 11.88 | 11.88
Sugru Black 8-Pack | Purchased | 21.99 | 1 | 21.99 | 21.99
U bolt | Purchased | 1.30 | 3 | 3.90 | 3.90
1 inch tee | Purchased | 1.34 | 12 | 16.08 | 16.08
1 inch PVC | Purchased | .40 per foot | 1 foot | .40 | .40

1 in to 1.5 in tee | Purchased | 2.17 | 2 | 4.34 | 4.34
1.5 in PVC | Purchased | .60 per foot | 5.66 feet | 3.38 | 3.38
Props and Task Totals | | | | $282.20 | $282.20
Grand Totals | | | | $1,225.99 | $558.76

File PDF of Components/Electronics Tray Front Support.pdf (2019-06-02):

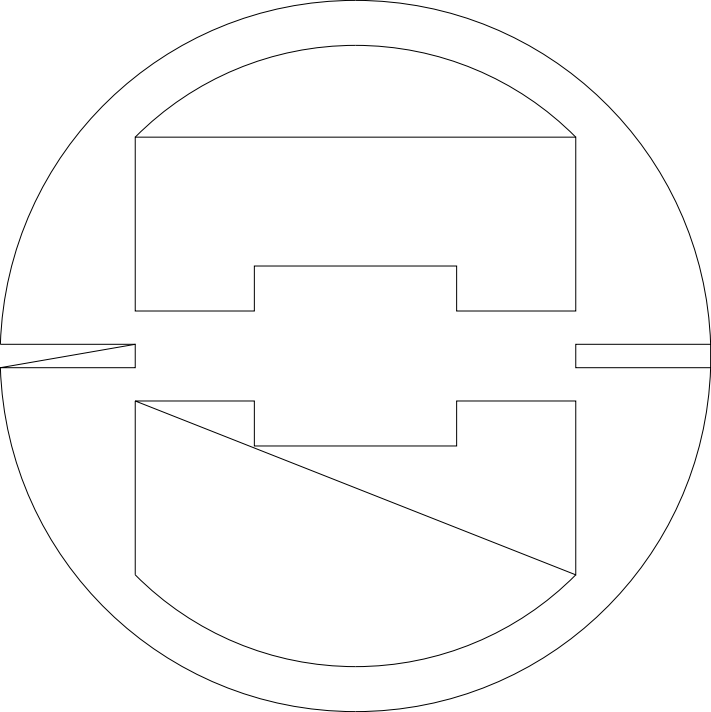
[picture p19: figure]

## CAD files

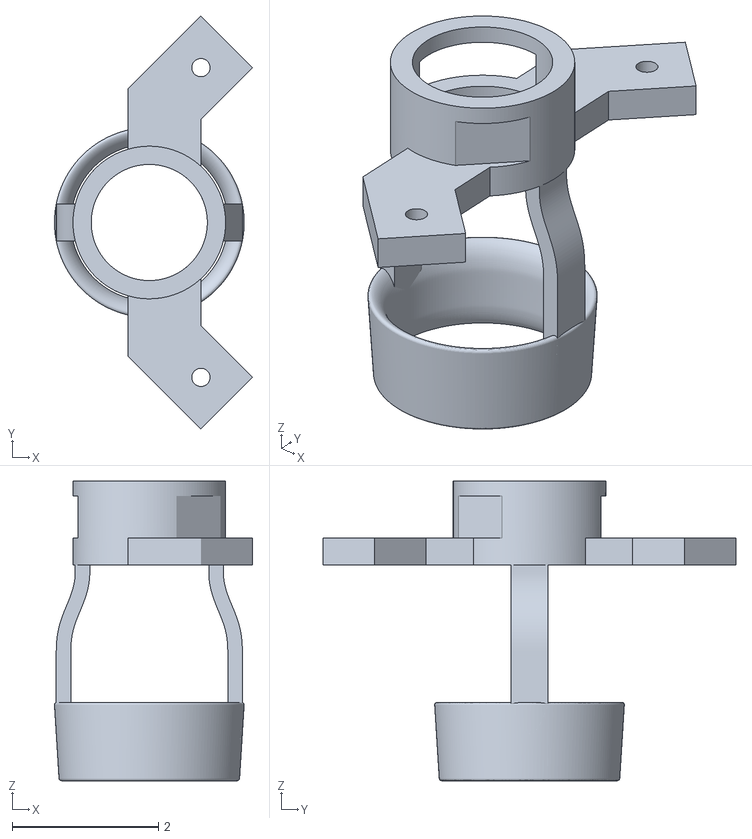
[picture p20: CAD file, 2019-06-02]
STL/Vertical Motor Mount full assembly.stl
2.71 x 5.66 x 4.10

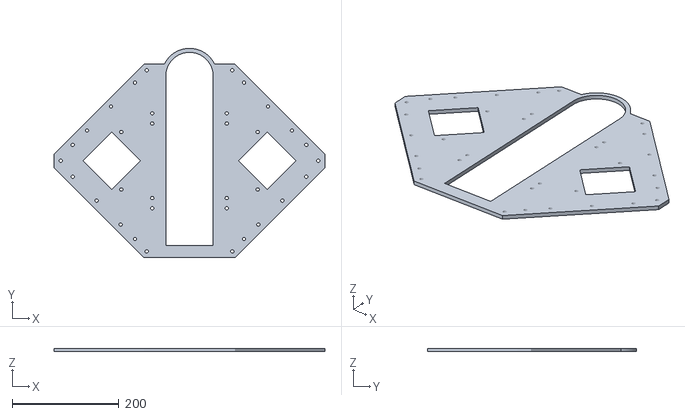
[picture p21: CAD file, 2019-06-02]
STL/Deck.stl
508.0 x 392.4 x 6.35

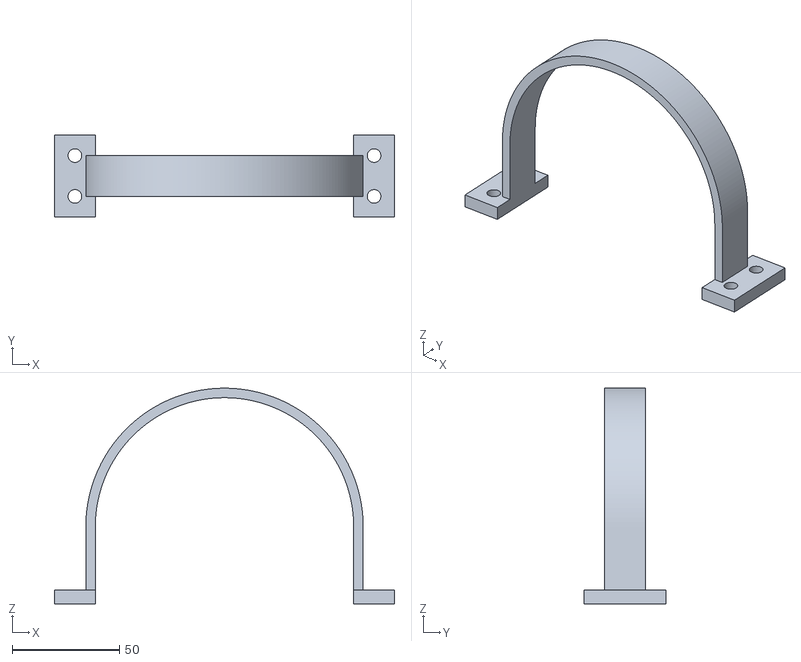
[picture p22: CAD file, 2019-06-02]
STL/Mount (1).stl
158.8 x 38.1 x 100.7

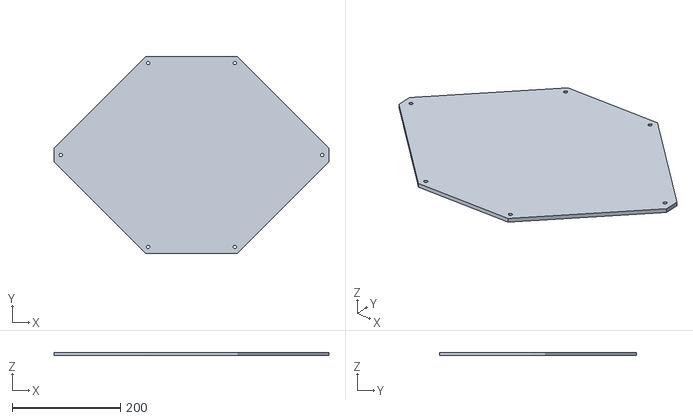
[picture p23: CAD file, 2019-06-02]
STL/Top Deck (never used).stl
508.0 x 363.2 x 6.35

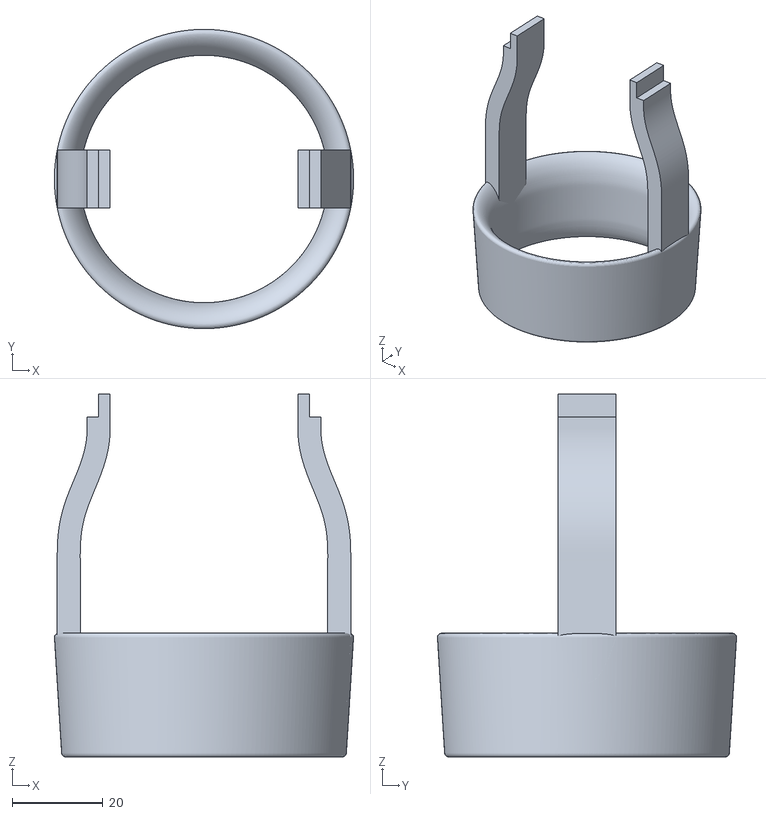
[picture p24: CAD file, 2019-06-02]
STL/Vertical Motor Mount part 2.stl
66.0 x 66.0 x 80.1

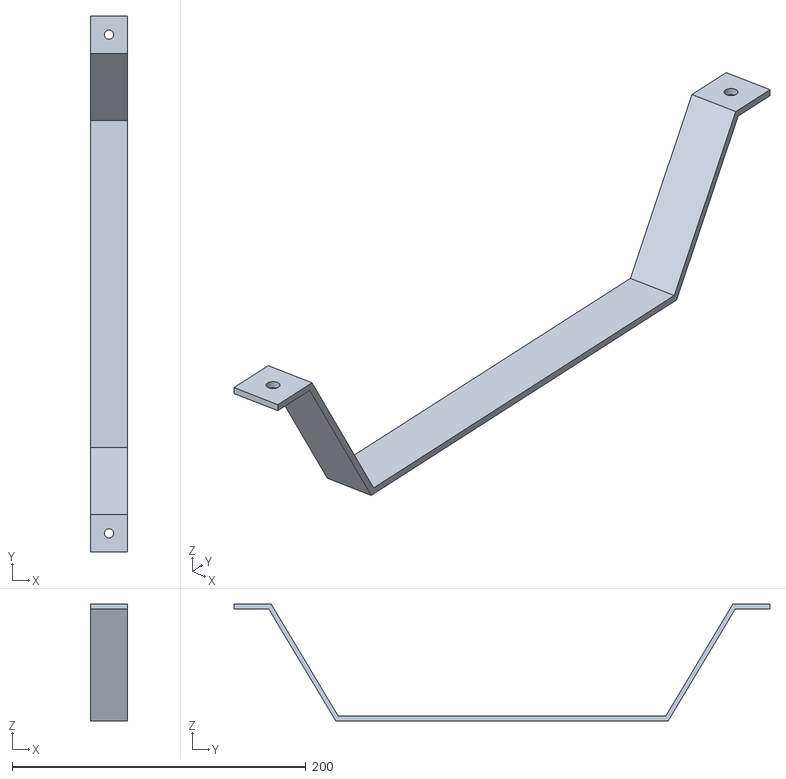
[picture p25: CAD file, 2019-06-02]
STL/Skids (1).stl
25.4 x 365.1 x 79.4

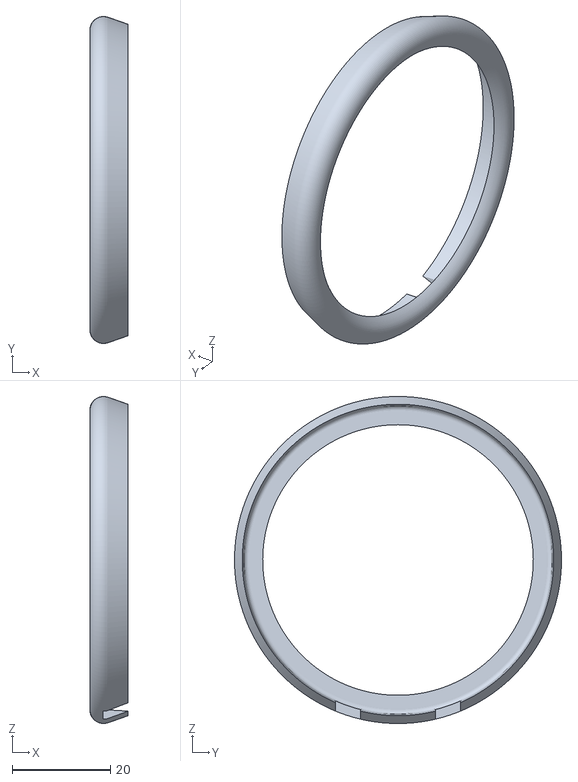
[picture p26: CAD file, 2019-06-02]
STL/Lateral Motor Mount Cover.stl
7.83 x 66.6 x 66.7

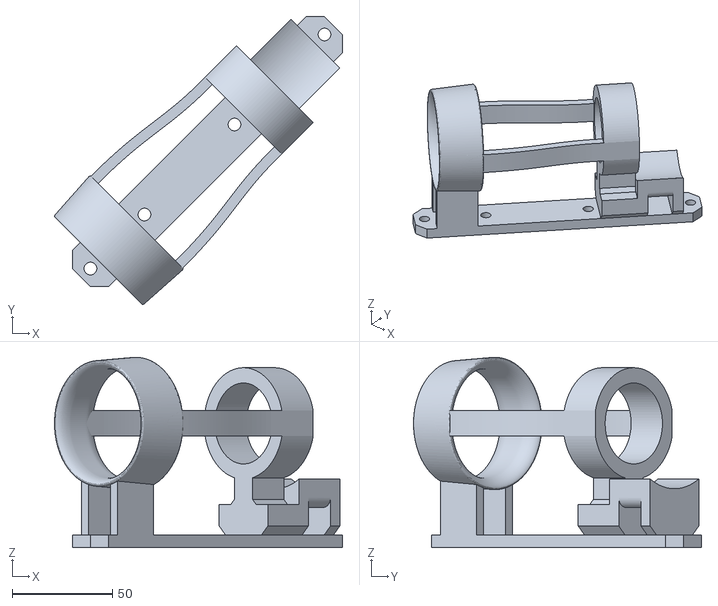
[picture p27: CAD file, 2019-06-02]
STL/Lateral Motor Mounts (R).stl
143.7 x 143.7 x 94.9

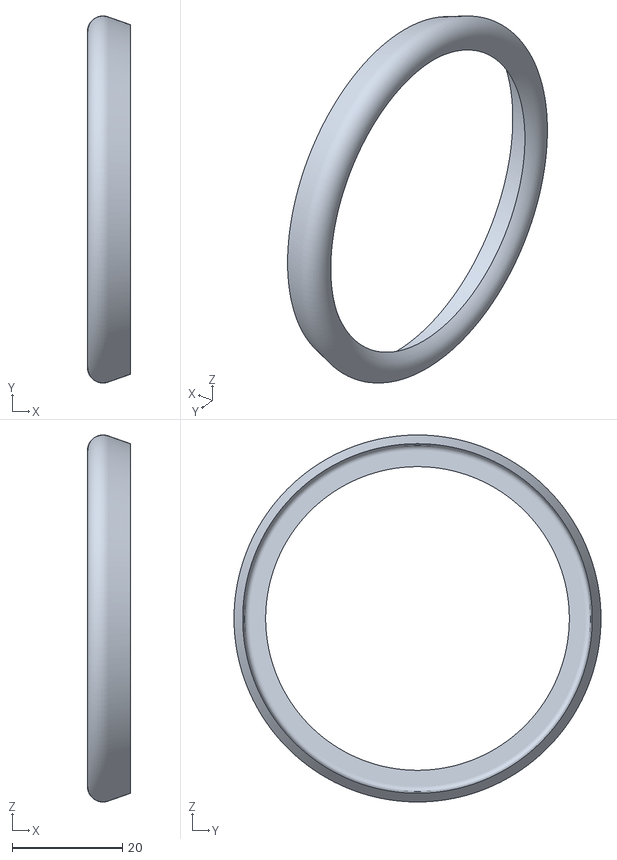
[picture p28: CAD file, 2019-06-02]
STL/Vertical Motor Mount Cover.stl
7.83 x 66.6 x 66.6

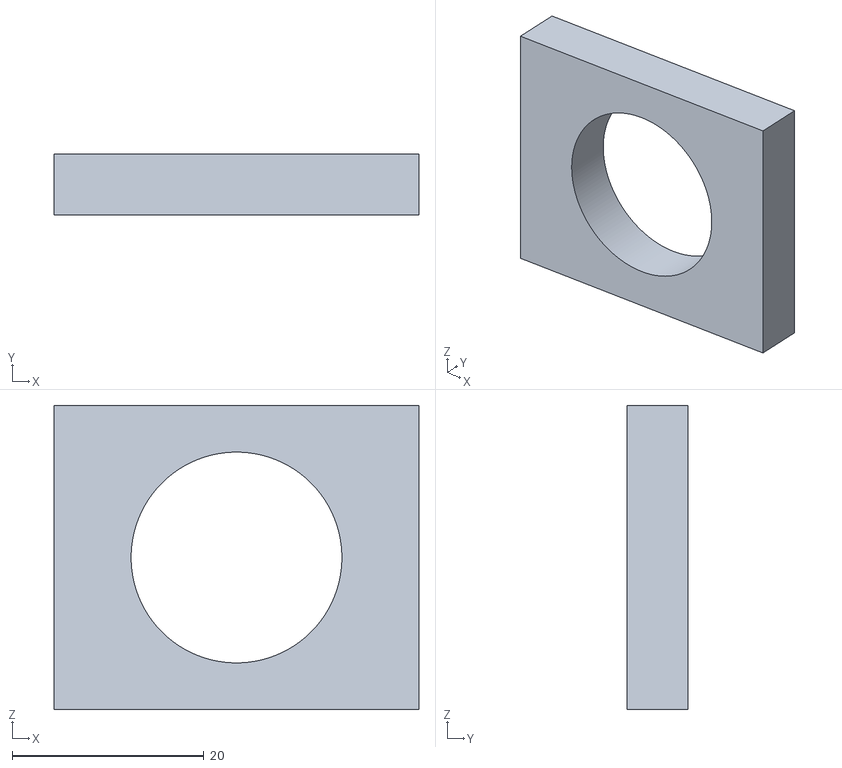
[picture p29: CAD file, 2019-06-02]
STL/Ball Bearing Mount.stl
38.1 x 6.35 x 31.8

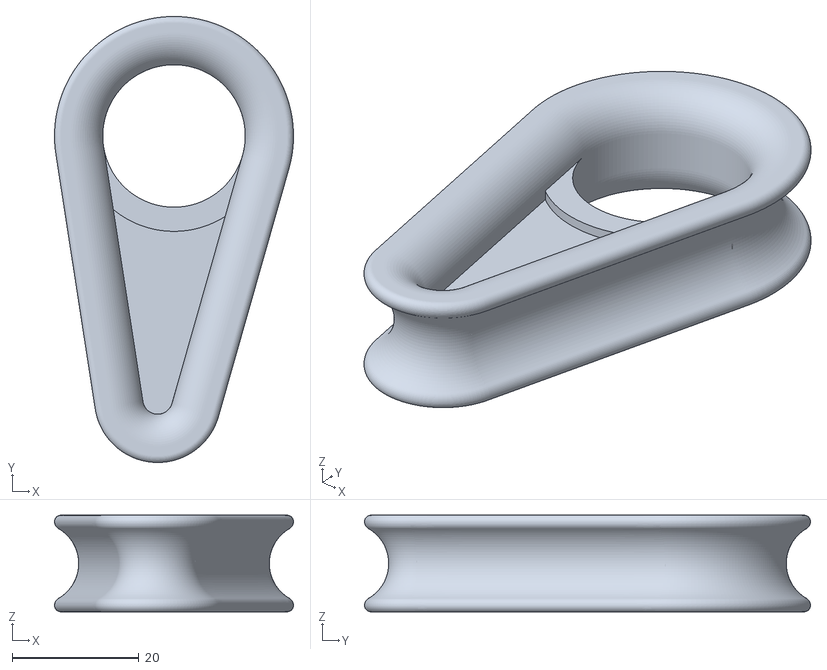
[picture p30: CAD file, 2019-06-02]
STL/Teather Thimble v1.stl
37.7 x 70.3 x 15.2

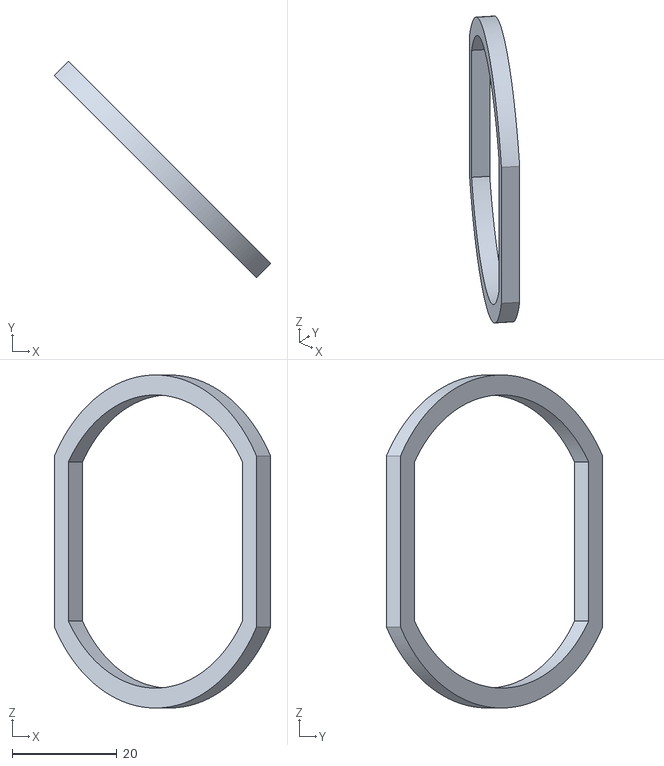
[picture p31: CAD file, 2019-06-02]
STL/Spacer.stl
41.3 x 41.3 x 63.6

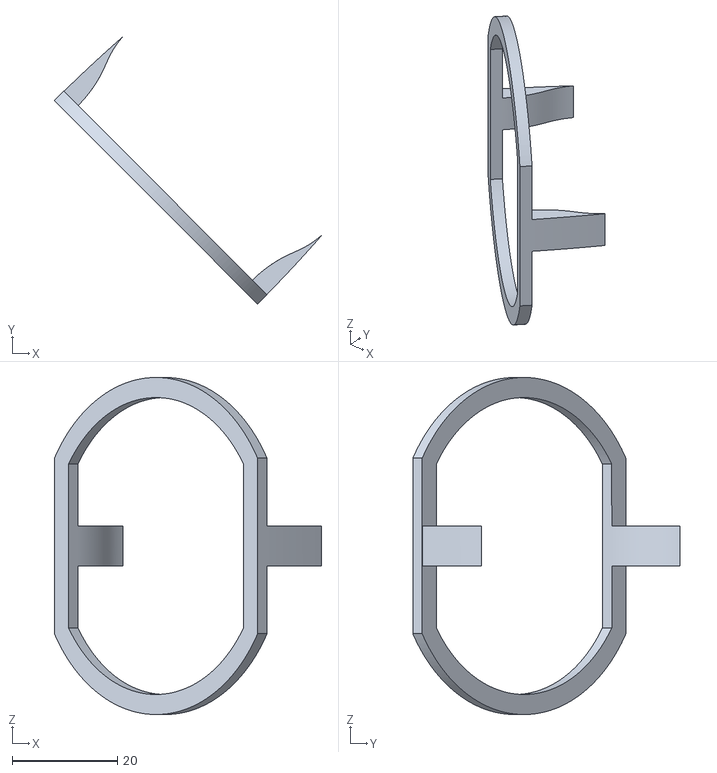
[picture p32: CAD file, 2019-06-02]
STL/Back Cover.stl
50.8 x 50.9 x 64.1

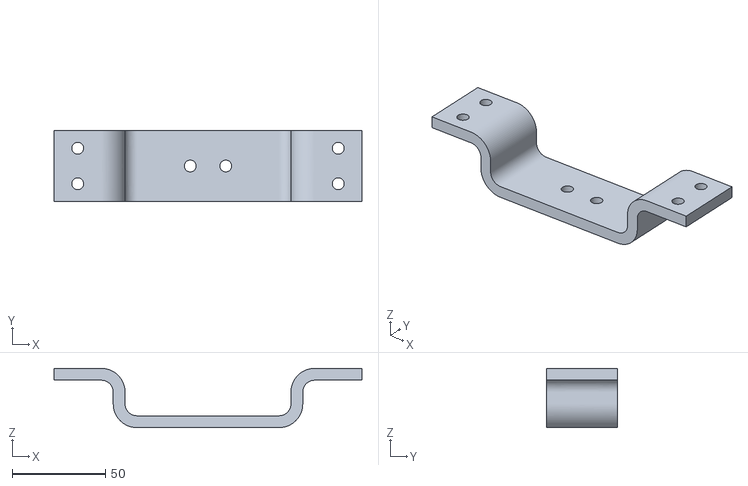
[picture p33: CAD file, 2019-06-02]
STL/Lower Deck Bracket.stl
165.1 x 38.1 x 31.7

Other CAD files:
STL/Claw Support.stl
STL/Vertical Motor Mount part 1.stl
STL/Lateral Motors Mounts (L).stl

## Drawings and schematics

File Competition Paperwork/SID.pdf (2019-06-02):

COMPUTER | XBOX CONTROLLER

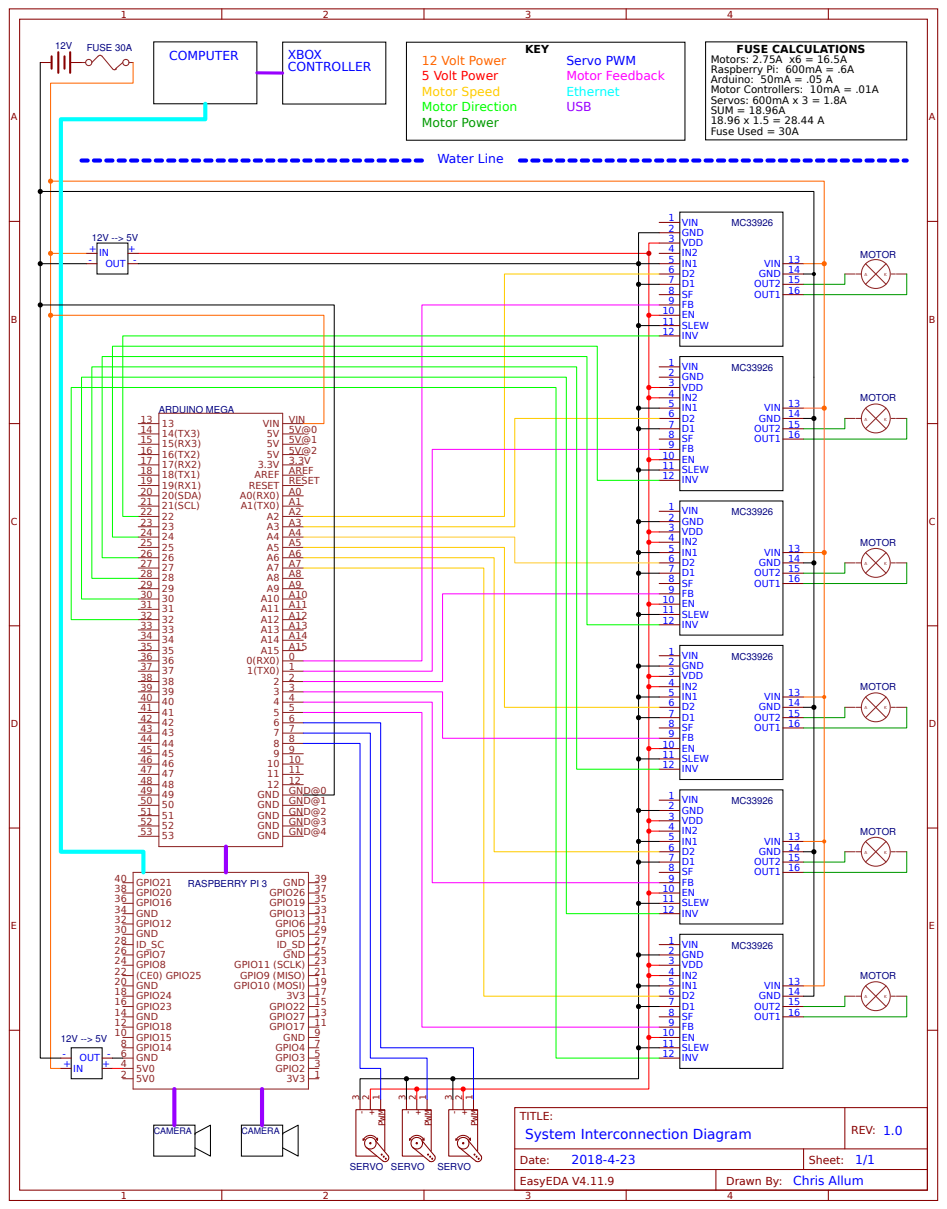
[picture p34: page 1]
TITLE:; System Interconnection Diagram; REV: 1.0; Date:; Sheet: 1/1; EasyEDA V4.11.9; Drawn By: Chris Allum; ARDUINO MEGA; RESET; GND; GND@4; GND@0; GND@1; GND@2; GND@3; AREF; 21(SCL) 21; 20(SDA) 20; VIN; RASPBERRY PI 3; 1 GPIO2; GPIO3; 5 GND 6; GPIO4; 7 GPIO14 8; 9 GPIO15 10; GPIO17; 11 GPIO18 12; GPIO27; 13 GND 14; GPIO22; 15 GPIO23 16; 17 GPIO24 18; GPIO10 (MOSI); 19 GND 20; GPIO9 (MISO); 21 (CE0) GPIO25 22; GPIO11 (SCLK); 23 GPIO8 24; 25 GPIO7 26; GPIO5; 29 GND 30; GPIO6; 31 GPIO12 32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

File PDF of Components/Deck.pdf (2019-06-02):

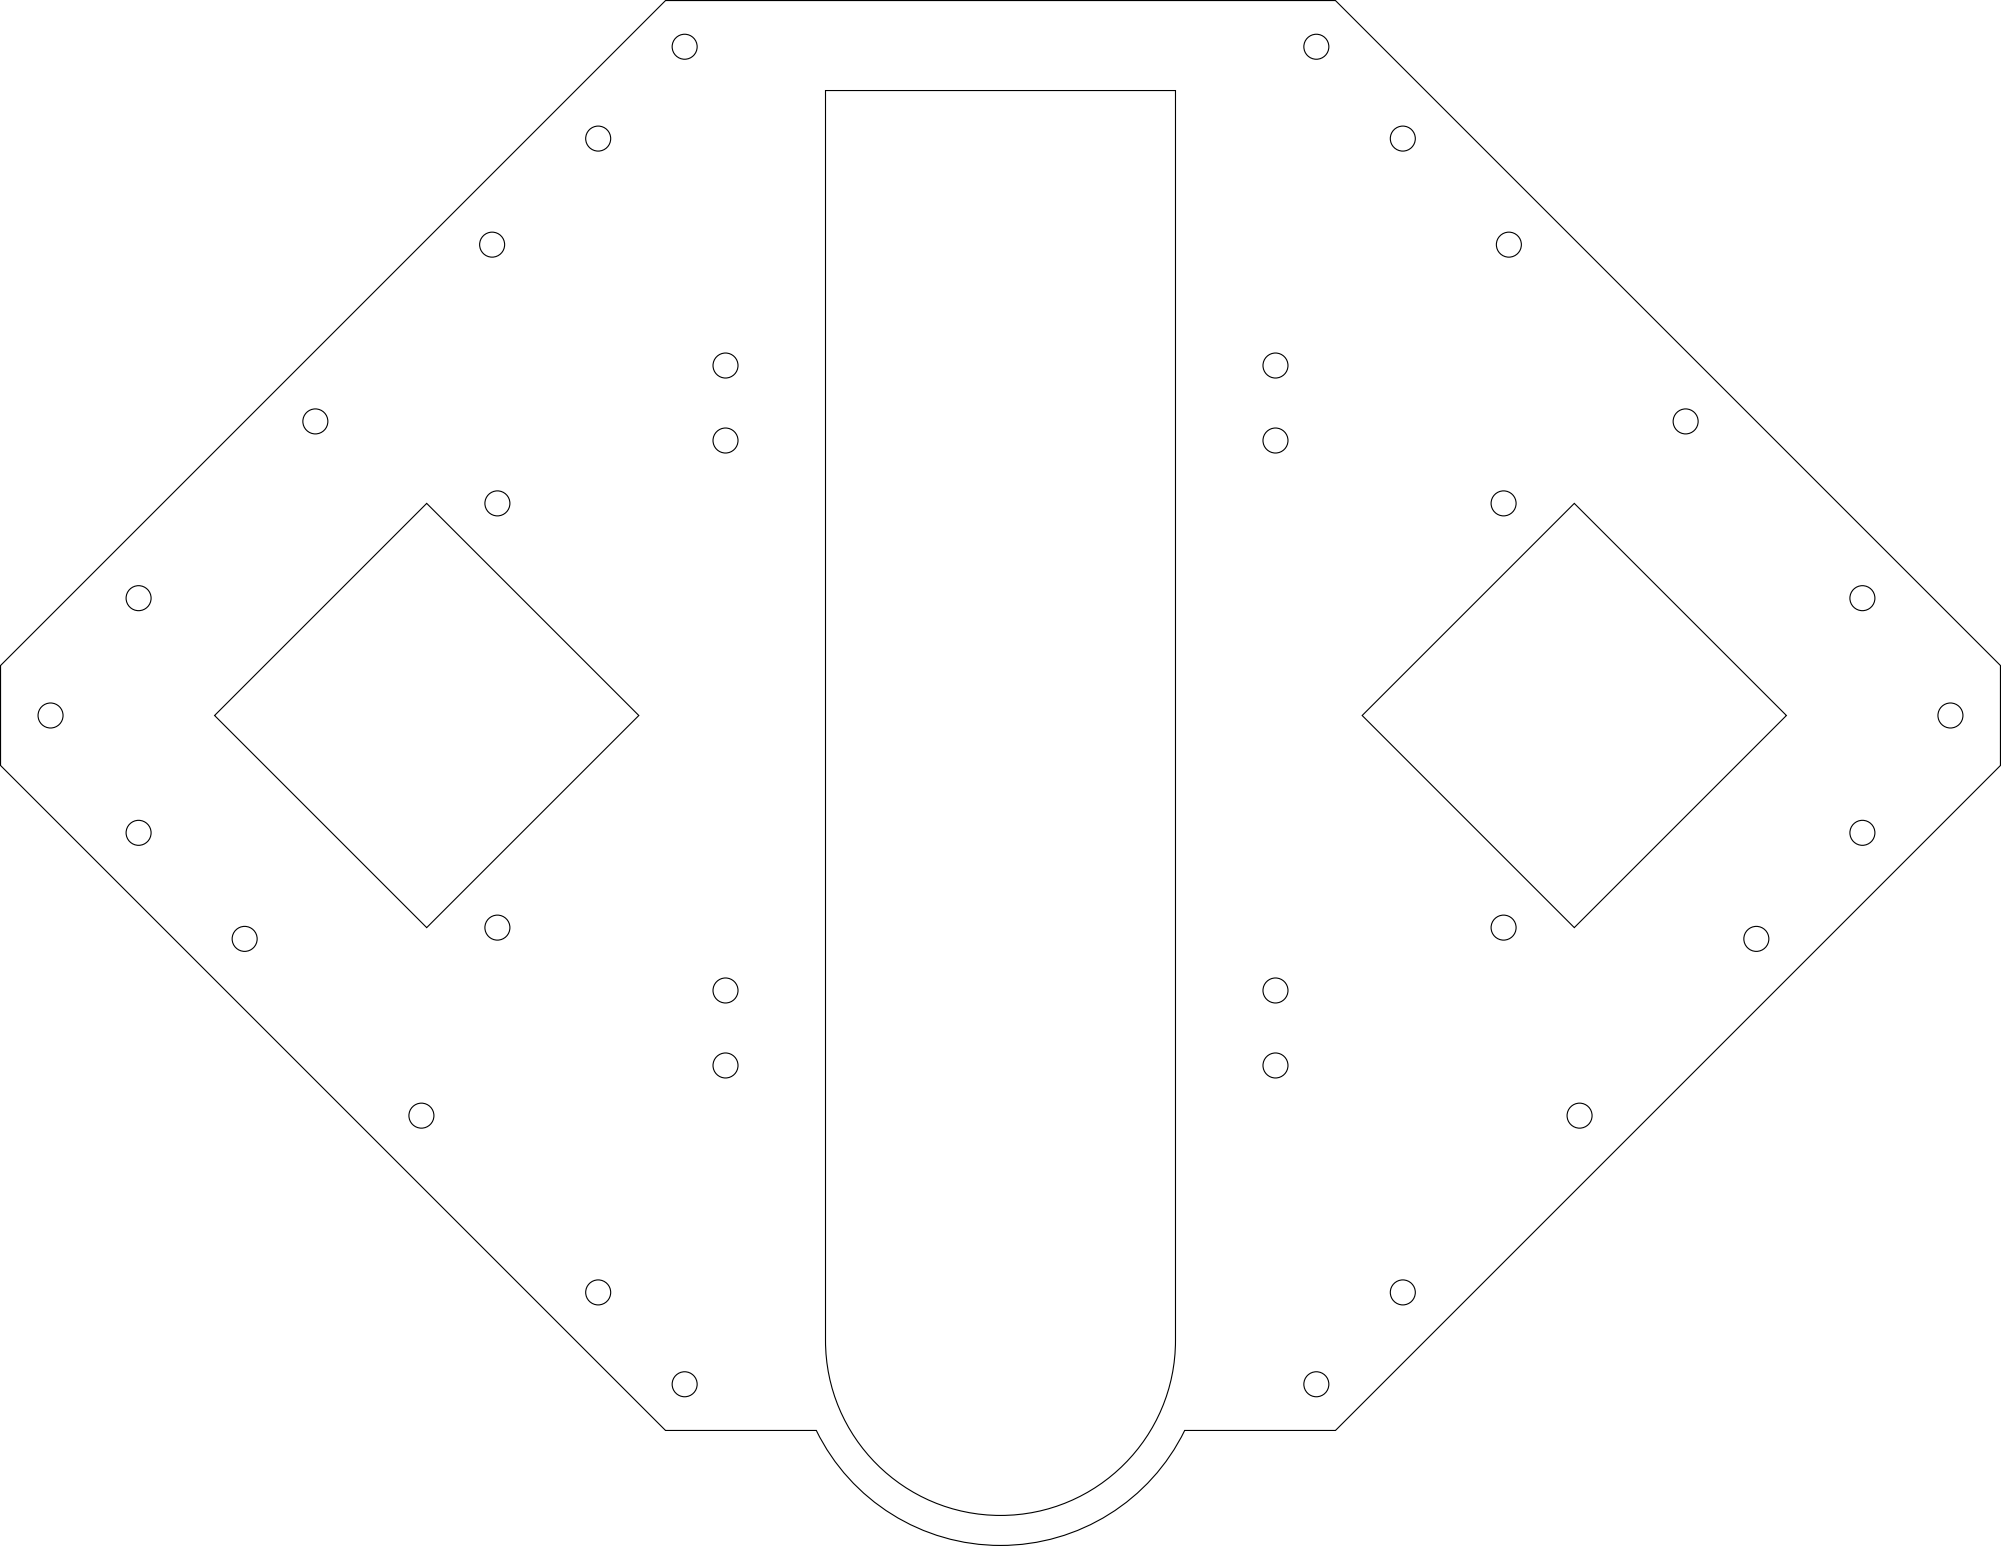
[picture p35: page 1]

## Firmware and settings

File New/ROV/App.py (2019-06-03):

# @auth: Chris Laporte
# @date: 9-28-2017
# @version: 2.0

#Imports
from flask import Flask, render_template, Response, request, url_for
#Test camera data for computer
### from camera import Camera
import time as t

### PI STUFF
### Pi camera
from camera_pi import Camera
from nanpy import (ArduinoApi, SerialManager, Servo)
import os
import sys



###### CONSTANTS ######
NUM_MOTORS = 6
#Pins changed to be fixed
thrustPins = [7,6,5,4,3,2] #Order: Fr L, Fr R, Ba R, Ba L, Vert1, Vert2
dirPins = [32,30,28,26,24,22]

clawPin = 8 
CLAW_MIN = 103
CLAW_MAX = 51

wristPin = 9

camPin = 11


#Declare flask app
app = Flask(__name__)

try:
        connection = SerialManager()
        print(str(connection))

        arduino = ArduinoApi(connection = connection)
        claw = Servo(clawPin)
        wrist = Servo(wristPin)
        cam = Servo(camPin)
        
except:
        print("Failed to connect to Arduino")

for i in range(0, len(thrustPins)):
        arduino.pinMode(thrustPins[i], arduino.OUTPUT)
        arduino.pinMode(dirPins[i], arduino.OUTPUT)

#Main Page
@app.route('/')
def index():
        return render_template('index.html')

def gen(camera):
        while True:
                frame = camera.get_frame()
                yield (b'--frame\r\n' b'content-Type: image/jpeg\r\n\r\n' + frame + b'\r\n')
#Video streaming route
@app.route('/videoFeed')
def videoFeed():
        return Response(gen(Camera()),mimetype='multipart/x-mixed-replace; boundary=frame')

#Read in motor data and write to Arduino
@app.route('/motorData')
def motorData():
        thrustValues = []
        dirValues = []
        for i in range(0, NUM_MOTORS):
                motor = "motor" + str(i)
                motorVal = request.args.get(motor)
                motorVal = int(motorVal)                
                if motorVal < 0:
                        dirValues.append(0)
                        thrustValues.append(0 - motorVal)
                else:
                        dirValues.append(1)
                        thrustValues.append(motorVal)
        print(thrustValues)
                

        try:

                #t.sleep(1)
                for i in range(0, NUM_MOTORS):
                        arduino.analogWrite(thrustPins[i], thrustValues[i])
                        arduino.digitalWrite(dirPins[i], dirValues[i])
        except:
                print("MOTORS NOT WORKING: ")
                print(thrustValues)
                #os.execl(sys.executable, sys.executable, *sys.argv)
                for i in range(0, NUM_MOTORS + 1):
                        arduino.analogWrite(thrustPins[i], 0)


        return ""


#Read in claw data and write to Arduino
@app.route('/clawData')
def clawData():

        

        try:
                wristName = "wristValue"
                wristValue = request.args.get(wristName)
                print(wristValue)
                wrist.write(wristValue)
        except:
                print("RIP")

        
        
        try:
                clawName = "clawValue"
                clawValue = request.args.get(clawName)
                #type(clawValue)
                #clawValue = int(clawValue)
                #try:
                print(clawValue)
                claw.write(clawValue)
        except:
                print("hello chris")
                '''
                print("CLAW NOT WORKING: ")
                print(str(clawValue))
                claw.write(CLAW_MAX)
                '''
        return ""
"""     

try:
	while True:
		for i in range(0, NUM_MOTORS):
            arduino.analogWrite(motorPin[i], thrustValues[i])

except:
    for i in range(0, NUM_MOTORS):
        arduino.analogWrite(motorPin[i], 0)
"""
if __name__ == '__main__':
        app.run(host='0.0.0.0', port=5000, debug=True, threaded=True)

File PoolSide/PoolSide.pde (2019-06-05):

/*
 * Processing code to take inputs and send them
 * over HTTP request to a server on the Rasp Pi
 *
 * @auth: Chris Laporte
 * @date: 4/10/18
 * @version: 2.56
 */

/////////////////UPDATE WITH CONTROLLER ADDING BUTTONS FOR CAMERA CONTROL

// IMPORTS
import http.requests.*; //HTTP library
import org.gamecontrolplus.gui.*;
import org.gamecontrolplus.*;
import net.java.games.input.*;



// Globals // 
ControlIO control; //Initializes the control library
ControlDevice xbox; //The control device

//CONSTANTS FOR TRIM
static float BACK_RIGHT_TRIM = 1;
static float BACK_LEFT_TRIM = 1;
static float FRONT_RIGHT_TRIM = 1;
static float FRONT_LEFT_TRIM = 1;
static float VERTICAL_R_TRIM = .9;
static float VERTICAL_L_TRIM = 1;


// Declare controller values
float leftStickX, leftStickY;
float rightStickX, rightStickY;
float leftTrigger, rightTrigger;
boolean leftBumper, rightBumper;


//Declare number of motors
int NUM_MOTORS = 6;
int NUM_HORIZ_MOTORS = 4;
int NUM_CLAW_STUFFS = 2;



//Create empty lists for current and previous motor values
int[] thrustValues; //Motor Thrust Values
int[] previousValues; //Old Motor Thrust Values



//Create the maxumum and minimum values for the claw
int CLAW_MIN = 100;
int CLAW_MAX = 50;



//Create the strating angle of the Swivil Cam and previous angle for swivil cam
int[] camAngles = {30, 60, 90, 120, 150, 180};
int camValue = 0;
int preCam = camValue;



//Create the current and previous claw values
int[] clawValues;
int wristValue;
int[] previousCValues;



//Create the pieces of the strings to send the data(URL and values)
String SERVER_PATH = "http://169.254.38.217:5000/";   //OLD IP: 169.254.175.59:5000
String MOTOR_PATH = "motorData?";
String CLAW_PATH = "clawData?";
String CAM_PATH = "camData?";
String camName = "swiValue=";
String[] varNames = {"motor0=", "motor1=", "motor2=", "motor3=", "motor4=", "motor5="};
//String clawName = "clawValue=";
String[] clawNames = {"clawValue=", "wristValue="};



//Create the value so that the single button claw and wrist works and does not trigger repeatedly while button is pressed
boolean preBumperPressed = false;
boolean preRBumperPressed = false;
boolean preStart = false;
boolean preSelect = false;


//Create values to store url
String sendString;
GetRequest get;



//Run once on startu[ of the program
void setup() {
  //set up the variables
  thrustValues = new int[NUM_MOTORS];
  previousValues = new int[NUM_MOTORS];
  //clawValue = CLAW_MAX;
  clawValues = new int[NUM_CLAW_STUFFS];
  clawValues[0] = CLAW_MAX;
  clawValues[1] = 10;
  previousCValues = new int[NUM_CLAW_STUFFS];
  //wristValue = 0;
  //previousClaw = clawValue;
  sendString = SERVER_PATH;



  //Create the window size
  get = new GetRequest(SERVER_PATH);
  size(600, 600);



  control = ControlIO.getInstance(this); // Initialize the ControlIO...idk what this really does
  xbox = control.getMatchedDevice("ROVConfig"); // Load the config file



  // make sure there is an xbox controller
  if (xbox == null) {
    
    println("Device not configured!");
    System.exit(-1);
    
  }
  
}



//Main body of program
void draw() {

  //create the window displaying the values
  background(0);
  stroke(255);
  parseControlValues();
  text("Back Right: " + str(thrustValues[0]), 25, 25);
  text("Back Left: " + str(thrustValues[1]), 25, 50);
  text("Front Right: " + str(thrustValues[2]), 25, 75);
  text("Front Left: " + str(thrustValues[3]), 25, 100);
  text("Vertical L: " + str(thrustValues[4]), 25, 125);
  text("Vertical R: " + str(thrustValues[5]), 25, 150);
  text("Claw: " + str(clawValues[0]), 25, 175);
  text("Wrist: " + str(clawValues[1]), 25, 200);

  // Only sends data if the data is different. More efficient
  for (int i = 0; i < NUM_MOTORS; i++) {

    if (thrustValues[i] != previousValues[i]) {
      
      sendString = sendString + MOTOR_PATH;

      for (int j = 0; j < NUM_MOTORS; j++) {
        
        sendString = sendString + varNames[j] + str(thrustValues[j]) + "&";
        
      }

      //send motor values
      get = new GetRequest(sendString);
      get.send();

      for (int k = i; k < NUM_MOTORS; k++) {
        
        previousValues[k] = thrustValues[k];
        
      }

      sendString = SERVER_PATH;
      break;
      
    }
    
  }

  //////////////////////////////////////////////////////////////////////////////////////////////////  
  /*
  //only send if claw value is different and send
  if (clawValue != previousClaw) {
    
    sendString = SERVER_PATH + CLAW_PATH + clawName + str(clawValue);
    previousClaw = clawValue;

    get = new GetRequest(sendString);
    get.send();

    sendString = SERVER_PATH;
    
  }
  */
  /////////////////////////////////////////////////////////////////////////////////////////////////////
  
  /*
  //set Swivil Cam Angle only send if defferent
  if (camValue != preCam) {
    
    sendString = SERVER_PATH + CAM_PATH + camName + str(camAngles[camValue]);
    preCam = camValue;
    
    get = new GetRequest(sendString);
    get.send();
    
    sendString = SERVER_PATH;

  }
  */
  
  /////////////////////////////////////////////////////////////////////////////////////////////////////

  //set wrist and claw only sends if values are different
  
  for (int i = 0; i < NUM_CLAW_STUFFS; i++) {
   
   if (clawValues[i] != previousCValues[i]) {
     
     sendString = sendString + CLAW_PATH;
   
     for (int j = 0; j < NUM_CLAW_STUFFS; j++) {
     
       sendString = sendString + clawNames[j] + str(clawValues[j]) + "&";
   
     }
   
   //send claw values
     get = new GetRequest(sendString);
     get.send();
   
     for (int k = i; k < NUM_CLAW_STUFFS; k++) {
     
       previousCValues[k] = clawValues[k];
   
     }
   
     sendString = SERVER_PATH;
     break;
   
   }
   
 }
  
}



    ////////////////////////////////////////////////////////////////////////////////////////////////////////////////////////////////
void parseControlValues() {
  getControlValues();
  float thrustConst = 0;
  float rotatConst = 0;

  if (getMag(leftStickX, leftStickY)+getMag(rightStickX, 0) > 0) {
    
    thrustConst = getMag(leftStickX, leftStickY)/(getMag(leftStickX, leftStickY)+getMag(rightStickX, 0));
    rotatConst = getMag(rightStickX, 0)/(getMag(leftStickX, leftStickY)+getMag(rightStickX, 0));
    
  }
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
